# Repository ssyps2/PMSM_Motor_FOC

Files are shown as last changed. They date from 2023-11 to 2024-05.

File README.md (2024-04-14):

## Diode Clamped Converter for Vehicle AC machine Drive

### Aim
The aim of this project is to simulate a 3-Phase Diode Clamped Inverter as a battery connected Permanent Magnet Synchronous Machine (PMSM) drive, and design a PCB to implement a low power version of this type of converter. The control algorithm will be tested in PLECS and eventually implemented in the F28379D micro-controller. Torque, speed, and mechanical position closed loop control of the PMSM motor will be included.

### Simulation
The main topology of the circuit for simulation in the PLECS is shown in Figure below.


### PCB Design
The circuit designed in the simulation will be implemented in a 4-layer Printed Circuit Board (PCB). Surface Mount Technology (SMT) will be applied for more compact layout, higher design flexibility, and reducing the noise interference. The microcontroller is selected to be TI’s LAUNCHXL-F28379D, which is a 32-bit MCU with frequency up to 200MHz and sufficient communication interface (like UART, CAN, I2C) and high-speed PWM channels. Also, current sensor will be used to detect the 3-phase current and sampled by ADC to complete the torque control loop.

The schematic of PCB is shown in Figure below.


The PCB layout is shown in Figrue below.
Diode_Clamped_Inverter_PCB

3D Model:
3D Model_1
3D Model_2

Diode Clamped Inverter:
Diode Clamped Inverter

### TimeTable


### Proposal
[Final Year Project Proposal - Pengyuan SHU.pdf](https://github.com/ssyps2/PMSM_Motor_FOC/files/14595623/Final.Year.Project.Proposal.-.Pengyuan.SHU.pdf)

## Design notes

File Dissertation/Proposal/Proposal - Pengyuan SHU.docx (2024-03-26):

# EEEE3001 / EEEE4008

# Final Year Individual Project Proposal

# Diode Clamped Converter for Vehicle AC machine Drive

AUTHOR: Mr. Pengyuan Shu

ID NUMBER: 20321149

SUPERVISOR: Dr. Alan Watson

MODERATOR: Dr. Gaurang Vakil

DATE: 25 October 2023

Project files and overall progress are available at:

https://github.com/ssyps2/PMSM_Motor_FOC

1. Overview
  1.1 Introduction

In the contemporary landscape characterized by a growing emphasis on clean and sustainable energy sources, the integration of battery-connected Permanent Magnet Synchronous Machine (PMSM) drives assumes a pivotal role across diverse applications, most notably in the domain of electric vehicles. These systems leverage the distinctive architecture of multilevel converters, enabling the generation of multi-level AC voltage waveforms sans the requirement of transformers. Diode Clamped Converter (DCC) is one of the types of multilevel topologies, which is commonly used as drives for high frequency motors as a result of their superior waveform quality [1]. This intrinsic characteristic empowers it to produce high-frequency AC voltages for the PMSM, characterized by notably diminished harmonic distortion. Consequently, the need for extensive filtering and the associated pulsations stemming from these harmonics is substantially reduced.

A fundamental aspect of the PMSM motor is its rotor, which comprises permanent magnets, thus obviating the need for magnetizing current. In this configuration, the motor's torque is solely generated by the stator current. Owing to this inherent efficiency, PMSM motors find widespread application in fields such as robotics and aerospace, where minimizing losses in the rotor is of paramount importance. The control of PMSM motors typically hinges on the Field Oriented Control (FOC) methodology, which can be used to control the AC quantities (voltage, current) [2, 3]. Against this backdrop, the primary focus of this project is to explore the integration of the Diode Clamped Converter into the PMSM drive [4]. For safety reasons, only low-power scenarios (2kW) will be considered. The potential ramifications of this endeavour extend to a wide array of domains, including electric vehicles, renewable energy systems, robotics, and beyond. The successful execution of this project bears the promise of delivering more efficient energy solutions, and in so doing, opens the door to fresh commercial opportunities and contributes to broader economic growth.

  1.2 Aim

The aim of this project is to simulate a 3-Phase Diode Clamped Inverter as a battery connected Permanent Magnet Synchronous Machine (PMSM) drive, and design a PCB to implement a low power version of this type of converter. The control algorithm will be tested in PLECS and eventually implemented in the F28379D micro-controller. Torque and speed closed loop control of the PMSM motor will be included.

  1.3 Objectives
A. Simulation

The main topology of the circuit for simulation in the PLECS is shown in Figure 1.

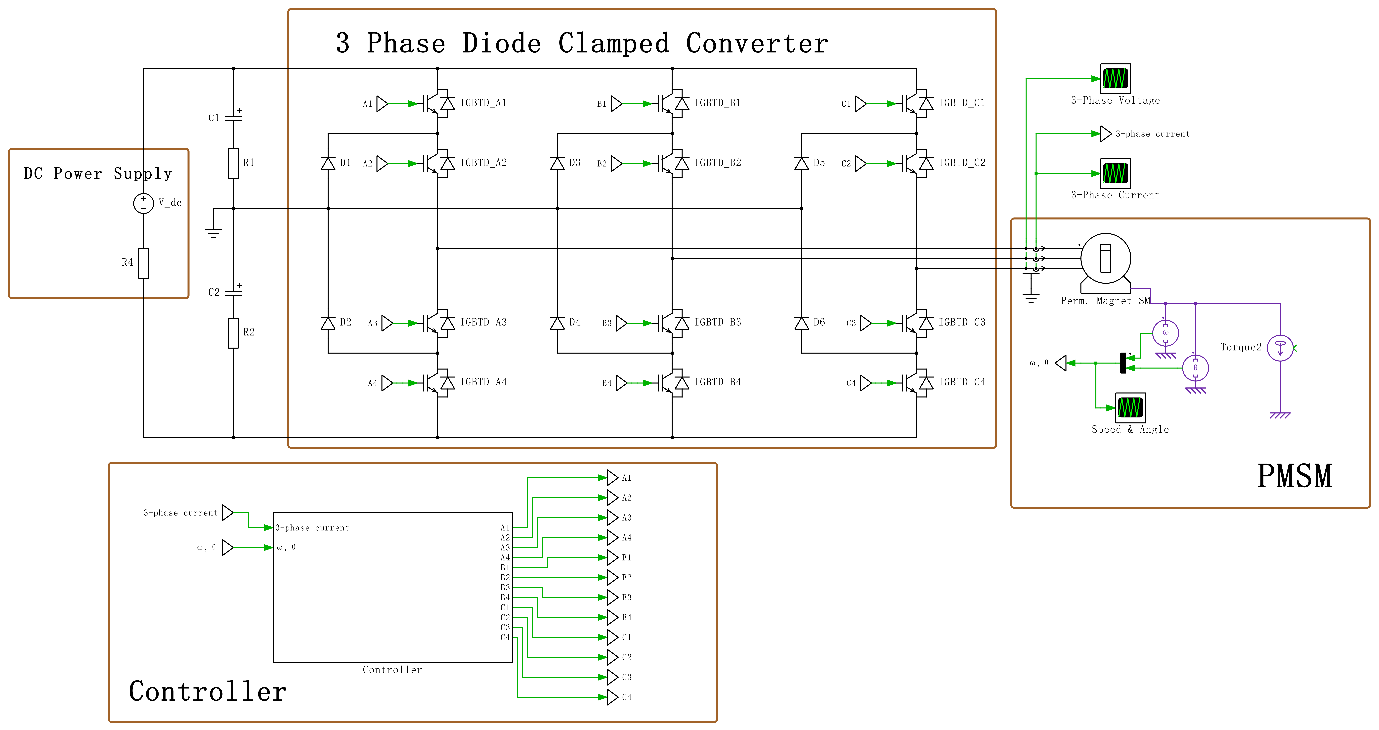
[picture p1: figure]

Figure 1. Main Topology for Simulation

B. PCB Design

The circuit designed in the simulation will be implemented in a 4-layer Printed Circuit Board (PCB), which is a medium used to integrate all the electrical components. Surface Mount Technology (SMT) will be applied for more compact layout, higher design flexibility, and reducing the noise interference. The microcontroller is selected to be TI’s LAUNCHXL-F28379D, which is a 32-bit MCU with frequency up to 200MHz and sufficient communication interface (like UART, CAN, I2C) and high-speed PWM channels. Also, current sensor will be used to detect the 3-phase current and sampled by ADC to complete the torque control loop.

2. Specification
  2.1 Software

The controller takes the 3-phase current and PMSM motor’s angle and speed as input, and output the PWM for each IGBT in the diode clamped converter. The controller contains two closed loops in series: torque loop and speed loop. The most fundamental loop is torque loop, which also can be referred to as current loop, as the torque of the PMSM motor is proportional to its stator current. This is where the FOC algorithm can be applied, combined with the PI controller to control the three-phase current in a closed loop to generate target torque based on the mechanical position of the rotor. Building upon the foundation of torque closed loop, the speed loop can be implemented by using the serial PI controller.

  2.2 Hardware

The specification for 3 phase PMSM motor would be like:

Power Rating | 2kW
Frequency Rating | 50Hz/60Hz
Supply Voltage | 300-320V

  2.3 Criteria for Success
a. PCB has no significant heating and vibration noise during operation.
b. Clear and correct 3 phase waveforms of both simulation and practical testing results.
c. Torque and speed of PMSM motor can be fully controlled by Qt-based HMI.
3. Methodology

No. | Goals and Processes | Challenges
1 | Read related resources to get familiar with the diode clamped converters and PMSM drives. | NA
2 | [Hardware] Select components according to the requirements (manufacturers can be Mouser, RS, Farnell…). The process is basically applying filter to exclude most irrelevant options, and compare those roughly fitted, then choose and order the best fit one (cheap / low loss / high tolerant…). | Some components might be unavailable / too expensive / take too long to ship
3 | [Hardware] Draw schematics based on selected components in KiCad, assign footprints to each component, and draw footprints that cannot found in the library. | Techniques for voltage balance between capacitors should be considered to prevent distortion.
4 | [Hardware] Plan PCB layout in KiCad, draw traces (ensure they are wide enough to handle large current) to connect components. Send project files to PCB factory for manufacturing. | Applying the design principles to reduce noise (should or should not use vias; thermal management on board; how to avoid ground bounce…)
5 | [Software] Whilst PCB is being manufactured, construct the diode clamped converter and the PMSM model in PLECS (fill up the parameters of PMSM simulation model according to the real machine model). | Mathematic modelling might be hard to implement; PMSM simulation model may not fit the real machine model well.
6 | [Software] Simulate the FOC algorithm and close the torque control loop in PLECS. Adjust the parameters to get expected output. | Implementation of FOC; Parameters of discrete PI controller might be difficult to tune.
7 | [Software] Further accomplish the speed closed loop control in PLECS. Adjust the parameters to get expected output. | Parameters tuning of discrete serial PI controller.
8 | [Hardware] Solder all the components to complete the converter construction, and test it with DC power source. | Small surface mount package components might be hard to solder on pads.
9 | [Software] Use Code Composer Studio (CCS) and Digital Power SDK to construct the embedded C code to implement the control algorithm on MCU, and validate simulation work with PCB connected to an RL load. | Task frequency will affect the parameters of PI controllers.
10 | Stretch target 1: Use the PCB to drive a low power PMSM motor with full FOC. | Realistic constrains of PMSM motor; Motor’s feedback data need to be logged and plotted.
11 | Stretch target 2: Design a Qt based human-machine interface (HMI) with a joystick for sending control commands to achieve torque and speed control of PMSM motor on a PC. | Delay might be occurred in data transmission, which will have negative impact on control.

4. Time Plan

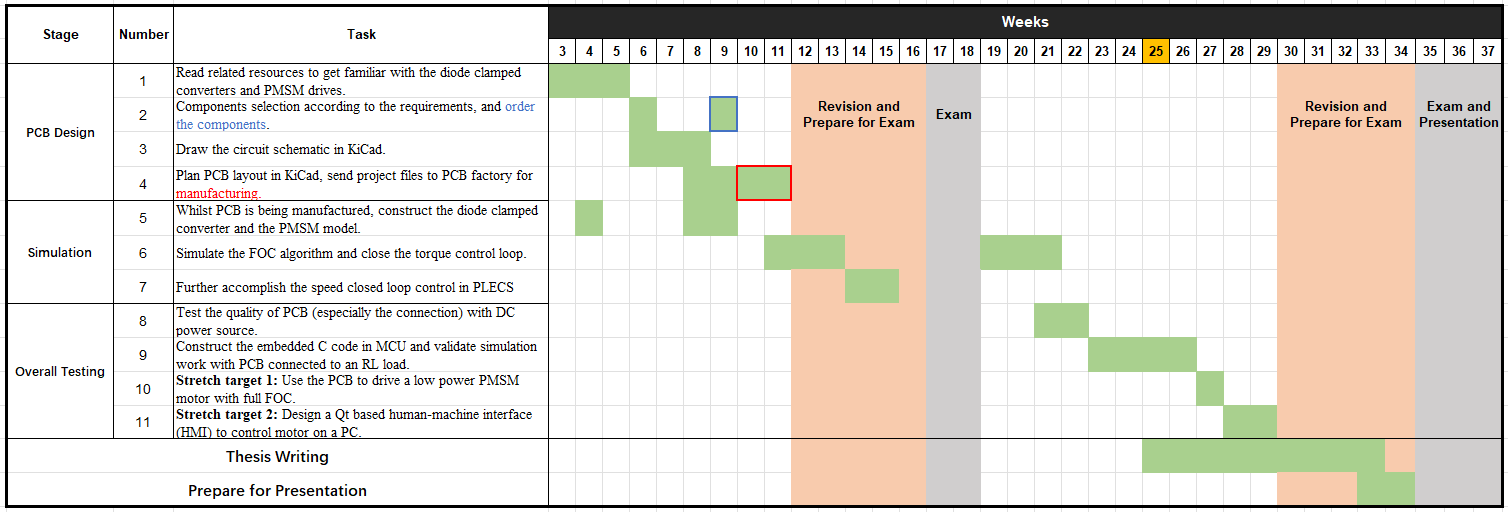
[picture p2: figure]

5. Reference

[1] B. Wu, “High Power Converters and AC Drives”, Wiley IEEE, 2nd Edition, 2016

[2] G. Abad, “Power Electronics and Electric Drives for Traction Applications”, Wiley, 2016

[3] A. Hughes “Electric Motors and Drives: Fundamentals, types, and applications”, 5th Edition, Elsevier, 2019

[4] S. N. Vukosavic, “Electrical Machines”, Springer, 2012

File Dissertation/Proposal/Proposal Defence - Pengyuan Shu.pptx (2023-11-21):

## Diode Clamped Converter for Vehicle AC Machine Drive

Pengyuan Shu (20321149)

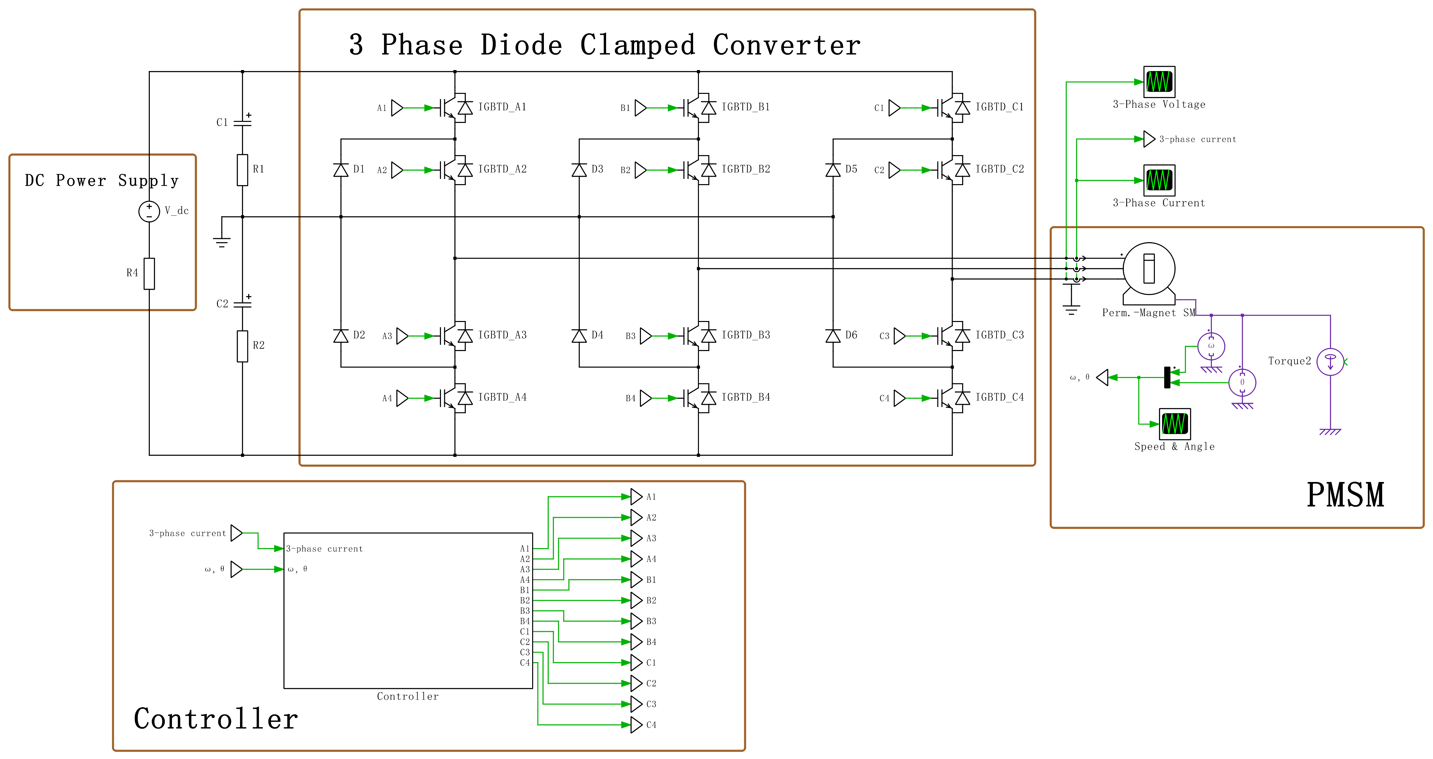
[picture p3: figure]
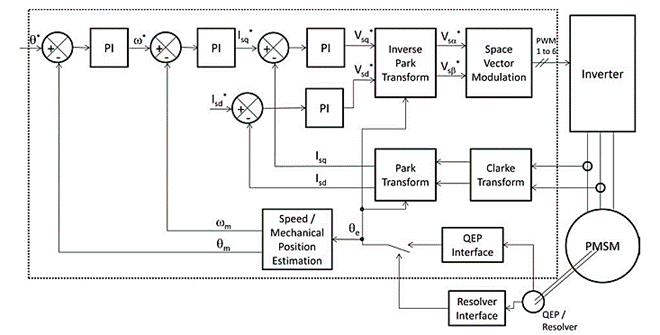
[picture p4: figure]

Circuit Topology

Control Diagram

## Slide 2

Methods and Approach

No. | Goals and Processes | Challenges
1 | Read related resources to get familiar with the diode clamped converters and PMSM drives. | NA
2 | Select components according to the requirements (manufacturers can be Mouser, RS, Farnell…). The process is basically applying filter to exclude most irrelevant options, and compare those roughly fitted, then choose and order the best fit one (cheap / low loss / high tolerant…). | Some components might be unavailable / too expensive / take too long to ship
3 | Draw schematics based on selected components in KiCad, assign footprints to each component, and draw footprints that cannot found in the library. | Techniques for voltage balance between capacitors should be considered to prevent distortion.
4 | Plan PCB layout in KiCad, draw traces (ensure they are wide enough to handle large current) to connect components. Send project files to PCB factory for manufacturing. | Applying the design principles to reduce noise (should or should not use vias; thermal management on board; how to avoid ground bounce…)
5 | Whilst PCB is being manufactured, construct the diode clamped converter and the PMSM model in PLECS (fill up the parameters of PMSM simulation model according to the real machine model). | Mathematic modelling might be hard to implement; PMSM simulation model may not fit the real machine model well.
6 | Simulate the FOC algorithm and close the torque control loop in PLECS. Adjust the parameters to get expected output. | Implementation of FOC; Parameters of discrete PI controller might be difficult to tune.
7 | Further accomplish the speed and mechanical position closed loop control in PLECS. Adjust the parameters to get expected output. | Parameters tuning of discrete serial PI controller.
8 | Solder all the components to complete the converter construction and test it with DC power source. | Small surface mount package components might be hard to solder on pads.
9 | Use Code Composer Studio (CCS) and Digital Power SDK to construct the embedded C code to implement the control algorithm on MCU and validate simulation work with PCB connected to an RL load. | Task frequency will affect the parameters of PI controllers.
10 | Stretch target 1: Use the PCB to drive a low power PMSM motor with full FOC. | Realistic constrains of PMSM motor; Motor’s feedback data need to be logged and plotted.
11 | Stretch target 2: Design a Qt based human-machine interface (HMI) with a joystick for sending control commands to achieve torque / speed / mechanical position control of PMSM motor on a PC. | Delay might be occurred in data transmission, which will have negative impact on control.

## Risk Table

Potential Risks | Mitigation Actions | Likelihood | Severity
PCB may not be manufactured as scheduled due to chip shortage or other unknown accidents. | Complete the schematic and PCB layout, then send them to factory for manufacturing early in the project. | Medium | High
Some key components are unavailable / shipping takes too long / too expensive. | Find alternatives, and identify those “long lead time” components | High | Low
The PCB may be damaged (e.g., burned), or contain a lot of noise interference due to design flaws. | Check the PCB layout with care (or ask supervisor for advice) before sending it to manufacture to prevent significant flaws. Adopt redundant design. Ensure the traces that can pass large current are wide enough. | Medium | High
Component size does not fit the package in the PCB. | Check the package size of each component before sending the PCB to manufacture. | Low | High
The performance of applied algorithm is less satisfactory. | Use MATLAB to evaluate the stability of the controller, modify it or adopt other controllers. | Medium | Medium

## Time Plan

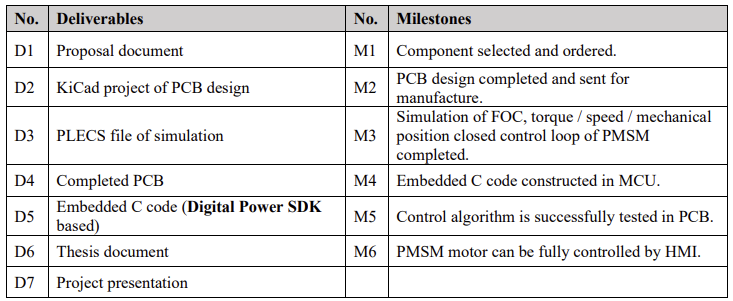
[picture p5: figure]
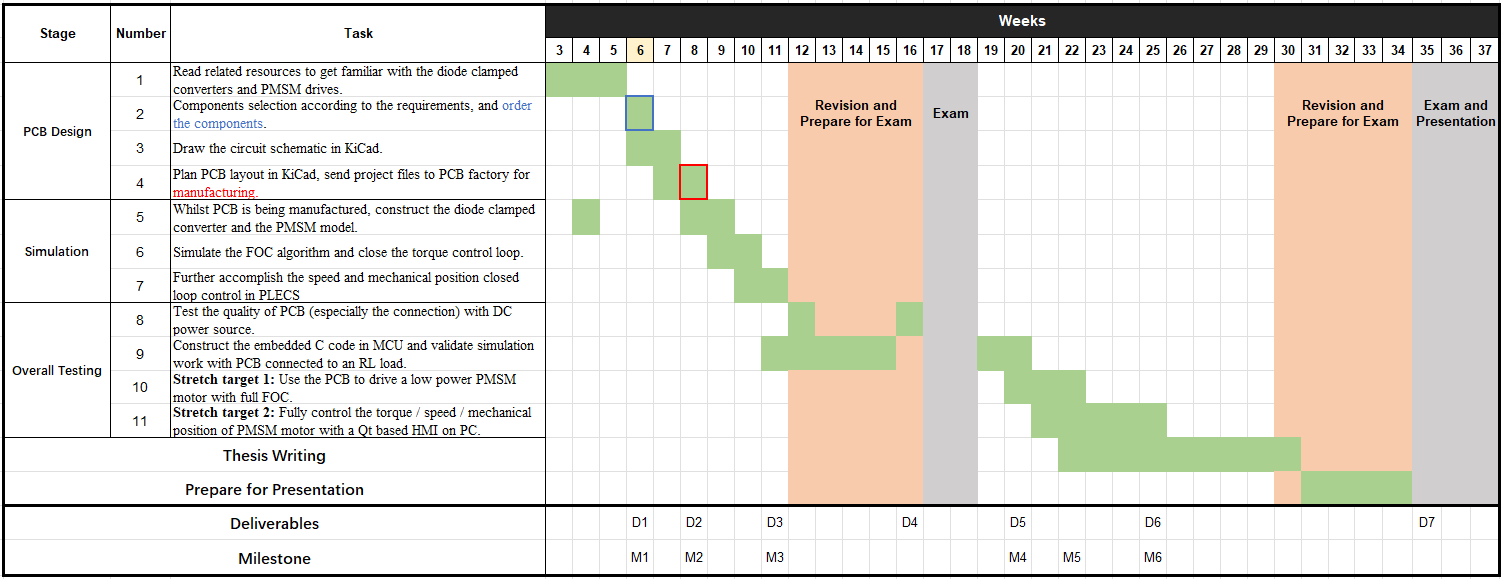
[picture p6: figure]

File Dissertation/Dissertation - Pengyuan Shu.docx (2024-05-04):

# EEEE3001

# Final Year Individual Project Dissertation

# Diode Clamped Inverter for Vehicle AC Machine Drive

AUTHOR: Mr. Pengyuan Shu

ID NUMBER: 20321149

SUPERVISOR: Dr. Alan Watson

MODERATOR: Dr. Gaurang Vakil

DATE: 9 May 2024

This third year project Dissertation is submitted in part fulfilment of the requirements of the degree of Bachelor of Engineering.

Table of Contents

Abstract (1 pages)

Chapter 1: Introduction (3 pages)

  1.1 Background and Summary of Literature Review

1.2 Aims and Objectives

Chapter 2: Simulation and Controller Design (15 pages)

2.1 Specifications of Tool Choice

2.2 PMSM Motor Modelling

2.3 Field-Oriented Control (FOC)

2.4 Topology Overview and Control Diagram

2.5 SPWM and SVPWM

2.6 Design of Controllers

Chapter 3: Hardware Design: Diode Clamped Inverter (6 pages)

3.1 Schematic

3.2 DC-Link Capacitance Calculations

3.3 Loss Calculations

3.4 PCB Layout

3.5 Physical Product

Chapter 4: Hardware Design: Control Board and its Peripherals (2 pages)

4.1 Schematic and PCB Layout

4.2 ADC Sampling

4.3 Physical Product

Chapter 5: Software Design: Implementation on MCU (6 pages)

5.1 Files Structure and IDE Configurations

5.2 Algorithm Implementation

Chapter 6: System Testing, Validation, and Analysis (8 pages)

6.1 Testing and Validation

6.2 Results Analysis

Chapter 7: Conclusion and Reflection (4 pages)

7.1 Consideration of System within Wider Context

7.2 Reflection on Management

References

Appendix

Abstract

Chapter 1: Introduction

  1.1 Background and Summary of Literature Review
    1.1.1 Introduction to PMSM

Permanent Magnet Synchronous Machines (PMSMs) are a class of electric motors that utilize permanent magnets embedded in the surface of the motor's rotor. This design is fundamental in creating a magnetic field that synchronizes with the rotating magnetic field of the stator. Efficiency is one of the distinguishing characteristics of PMSMs; the permanent magnets provide a steady magnetic field without the stator current, which is normally needed in other kinds of motors to maintain the field via the rotor windings.

The PMSM stands out for its high-power density, which is the amount of power generated per unit volume of the motor. This feature is particularly beneficial in the applications where space and weight are constrained, such as in automotive or aerospace industries. Another advantage of PMSMs is their high operational efficiency throughout a wide range of speeds and loads. This adaptability is complemented by their remarkable torque-to-weight ratio, which allows them to produce more torque per unit of motor weight than many other motor types. Moreover, PMSMs are also noted for their quiet operation and low maintenance requirements due to the lack of brushes and slide rings, which are prone to wear and strain.

The PMSM's torque generation capability is a direct consequence of the electromagnetic interaction between the stator's rotating magnetic field and the rotor's permanent magnets. This interaction produces torque that is precisely controllable, which is why PMSMs are ideal candidates for variable speed and position control applications.

    1.1.2 Introduction to Diode Clamped Inverter

The diode clamped inverters, also known as Neutral Point Clamped (NPC) inverters, can convert direct current (DC) to alternating current (AC) in a variety of applications. They are characterized by their multilevel output, which can generate voltage waveforms with steps at several voltage levels, not just the two levels produced by traditional two-level inverters. This ability to approximate sinusoidal waveforms more closely results in lower total harmonic distortion (THD). Due to their superior waveform quality, these types of inverters are commonly used as the drives for high frequency motors [1]. This intrinsic feature enables it to generate high-frequency AC voltages for the PMSM with significantly less harmonic distortion, and thus, the pulsations caused by these harmonics is significantly reduced.

In the three-phase diode clamped inverter topology, each phase leg includes several power semiconductor switches (could be MOSFET or IGBT) and clamping diodes. The clamping diodes are critical components that allow the inverter to maintain the voltage balance of the DC-link capacitors during operation, thereby ensuring the generation of the desired multi-level AC waveform. In this project, a three-phase three-level diode clamped inverter is used as the drive of PMSM motor, the topology is shown in the Figure 1.1 below. Three-level means each phase of the inverter can generate three different levels of voltage, which are +V_(dc) /2 , 0V, and -V_(dc) /2 .

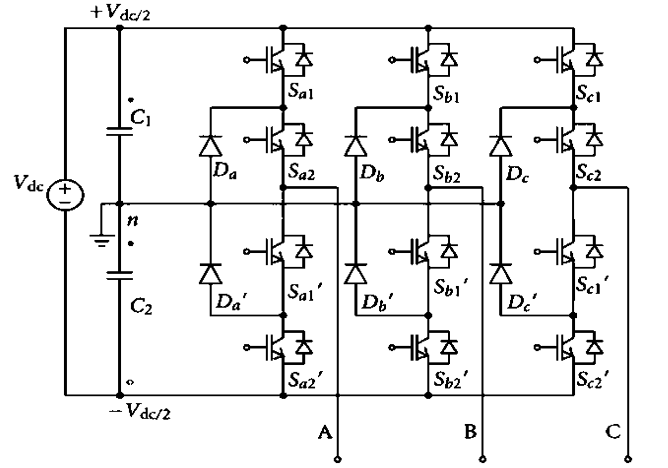
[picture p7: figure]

Figure 1.1 Topology of Three-Phase Three-Level Diode Clamped Inverter

    1.1.3 Field-Oriented Control (FOC)

Field-Oriented Control (FOC), also known as vector control, is an advanced method of motor control that treats the electric motor as a controllable entity in two orthogonal components [2, 3]. This control technique allows for separate control of the magnetic flux and torque in AC machines (such as PMSM), by aligning the reference frame of the control system with the vector space of the motor’s magnetic field. Essentially, FOC decouples the PMSM's torque and magnetic flux into two independent variables that can be controlled as if the motor were a direct current (DC) motor.

    1.1.4 Review of Existing Technologies and Developments

Inverter technology has advanced significantly, especially in the area of electric vehicle (EV) propulsion. Innovations in semiconductor materials, such as Silicon Carbide (SiC) and Gallium Nitride (GaN), have been critical in spawning a new generation of inverters. These new inverters offer increased power densities and efficiency, as well as the extraordinary ability to perform optimally at high frequencies and temperatures. The consequence is a significant reduction in the physical bulk and weight of inverter systems, as well as an increase in their dependability and operational lifespan.

Meanwhile, for control algorithm, there is also a technique called sensorless control, which eliminate the need for physical sensors in the motor by using estimators and observers to infer the rotor position. However, due to the complexity of algorithm, and issue of robustness, it would not be covered in this report.

  1.2 Aims and Objectives

The aim of this project is to achieve current and speed control of the PMSM motor (300V, BSM90N-175) through a three-phase three-level diode clamped inverter in PLECS and in reality. The inverter is controlled by TI’s F28379D Launchpad. For safety concerns, only low power situation (2kW) would be considered.

The project can be divided into following stages:

Stage 1: Initial Simulation of FOC in PLECS

Aim:

Create a mathematical model of PMSM motor in PLECS, and implement FOC in PLECS to verify the minimum acceptable capacitance of the DC-link capacitors.

Objectives:

- Work out the mathematical model of BSM90N-175 motor.
- Learn the working principles of Field-Oriented Control, build the continuous control model in PLECS.
- Change the target torque current to verify the performance of the two DC-link capacitors with calculated capacitance value, then work out the minimum acceptable value of capacitance and find the most suitable capacitor on the market.

Stage 2: Hardware Design in KiCad and Manufacturing

Aim:

Design a four-layer printed circuit board (PCB) for the three-phase three-level diode clamped inverter, as well as design a two-layer PCB for the control board (F28379D Launchpad) and its peripherals.

Objectives:

- Selection of components, build bill-of-materials (BOM) lists for purchasing.
- Schematic of the control board and the board of diode clamped inverter in KiCad, which includes gate drive circuit, ADC sampling circuit, connectors, etc.
- PCB layout in KiCad.

Stage 3: Controller Design in PLECS and MATLAB

Aim:

Design the continuous PI controller of speed, DC voltage balancing, and d-axis and q-axis current in MATLAB, convert them to discrete controllers and test in PLECS.

Objectives:

- Transfer functions of these continuous PI controllers from the “sisotool” in MATLAB.
- Convert the continuous PI controllers to discrete PI controllers.
- Test the discrete PI controller in PLECS.
- Convert the function blocks to “c-script” blocks in PLECS.

Stage 4: Software Design in Code Composer Studio (CCS)

Aim:

Convert the control algorithm and overall logic in PLECS file to C code that can be built and loaded on TMS320F28379D micro-controller, then test the program in real PMSM motor to verify the current and speed control.

Objectives:

- Configurate the environment of CCS, including file search path, library search path, predefined symbols, optimization configurations, etc.
- Construction of CCS program, which includes ADC sampling, motor encoder decoding, PI controller implementation, timer interruption, SPWM generation, etc.
- Test the program in real BSM90N-175 motor with the two PCBs to verify the speed and current control.

Chapter 2: Simulation and Controller Design

2.1 Specifications of Tool Choice

PLECS (Piecewise Linear Electrical Circuit Simulation) is chosen to be the tool of circuit simulation. It is a better choice than MATLAB in simulating electrical circuits for following reasons:

- PLECS can offer faster simulation times due to its optimized solvers.
- PLECS can offer real-time simulation capabilities for hardware-in-the-loop (HIL) testing. This feature is useful for testing the control logic on actual hardware before deployment.
- PLECS provides integrated thermal modelling, which enables the simulation of temperature-dependent behaviours of components and systems.

However, PLECS is not a suitable tool for controller design. For PI controller design, a tool named “sisotool” in MATLAB is used, which is an interactive graphical user interface (GUI) tool for designing and analysing single-input, single-output (SISO) control systems. It offers a variety of plotting functions, including bode plots, root locus, and step response plots, which are essential for understanding the frequency and time domain characteristics of the system.

2.2 PMSM Motor Modelling

The model is chosen to be ABB’s BSM90N-175. The electrical and mechanical parameters of this motor are shown in Table 2.1 below.

Table 2.1 Parameters of BSM90N-175 Model

Rated Speed (at 300 V) | 4000 rpm
Torque Constant K_t | 0.853 Nm/amp
Stator Resistance R_s | 1.24 ohms
Stator Inductance L_s | 4.15 mH
Pole Pairs p | 4
Inertia J | 3.389 Kg- cm^2

The electrical model of PMSM in PLECS is modelled by:

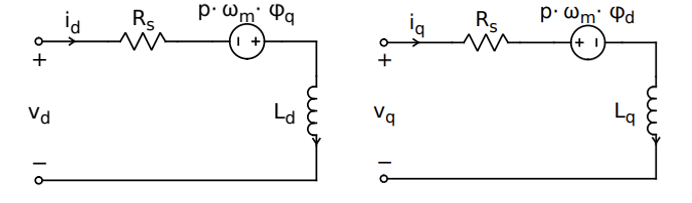
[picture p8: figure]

Figure 2.1 Electrical Model of PMSM in PLECS (left: d-axis; right: q-axis)

The stator flux linkages are given by:

φ_q =L_q i_q Eqn.2.1

φ_d =L_d i_d +φ_m^(') Eqn.2.2

where the symbol φ_m^(') represents the constant flux linkage, the symbol L_d and L_q represent stator inductance in d-axis and q-axis.

The three-phase stator currents are transformed to the two-dimensional rotating reference dq-frame, which converts an AC system into an equivalent DC system. This enables the use of traditional PI controllers with zero steady-state error. According to Figure 2.1, the stator voltage in d-axis and q-axis are given by:

V_d =R_s i_d -pω_m φ_q +L_d (di_d)/(dt) Eqn.2.3

V_q =R_s i_q +pω_m φ_d +L_q (di_q)/(dt) Eqn.2.4

Due to the AC motor is a synchronous machine with surface-mounted magnets and no saliency, flux lines are distributed evenly around the stator, which means that the motor's inductance measured in the direction of the d-axis and the q-axis will be the same. Thus:

L_q =L_d Eqn.2.5

This equality leads to a simplified Field-Oriented Control algorithm, because the current-regulating controller does not have to compensate for differences in inductance in different orientations of the rotor. As they are equal, L_q and L_d can be represented by L_s . Thus, Eqn.2.3 and Eqn.2.4 can be rearranged as:

V_d =R_s i_d -ω_e L_s i_q +L_s (di_d)/(dt) Eqn.2.6

V_q =R_s i_q +ω_e (L_s i_d +φ_m^(') )+L_s (di_q)/(dt) Eqn.2.7

where the electrical rotor speed ω_e =pω_m .

Moreover, according to the manual of PLECS, electromagnetic torque T_e and mechanical rotor speed ω_m of PMSM model in PLECS are given by:

T_e =3/2p(φ_d i_q -φ_q i_d ) Eqn.2.8

ω_m =1/J(T_e -Bω_m -T_m ) Eqn.2.9

ω_m =θ_m Eqn.2.10

where the symbol B represents the friction coefficient.

The configurations of initialising PMSM in PLECS are presented in Figure 2.2 and Figure 2.3 below, whose data are referred from the datasheet of BSM90N-175 motor. The model of PMSM is chosen to be “Rotor reference frame”, as it can decouple the motor’s flux and torque. In addition, the friction coefficient is assumed to be zero for simplification.

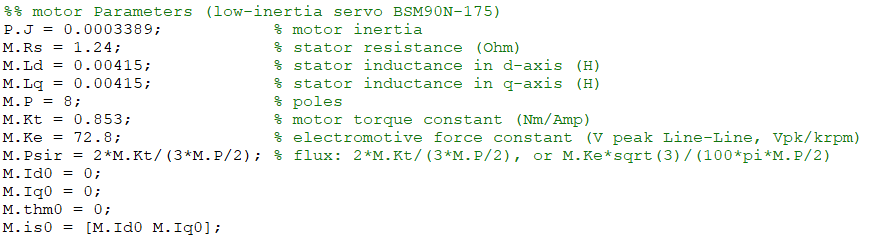
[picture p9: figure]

Figure 2.2 C-Code for Simulation Parameter Initialization in PLECS

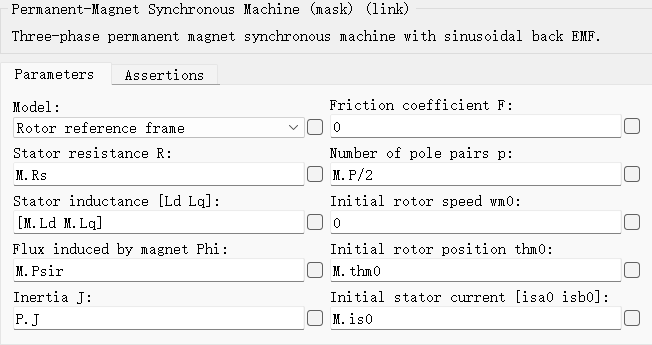
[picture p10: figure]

Figure 2.3 Configurations of PMSM Model in PLECS

2.3 Field-Oriented Control (FOC)

Field-Oriented Control is a control technique used in variable frequency drives to control the torque (and thus speed and position) of three-phase AC electric motors by controlling the current components independently. The essence of this algorithm is to decompose the stator currents into two orthogonal components that can be controlled separately: one aligns with the rotor's magnetic field (direct axis, or d-axis), and the other is perpendicular to it (quadrature axis, or q-axis). This decomposition allows the control system to adjust the torque and magnetic flux of the motor independently, like DC motor, which is easier to control because torque is directly controlled by armature current.

The procedures of FOC are demonstrated as follows:

1. Sample the phase currents of PMSM and get I_a , I_b , and I_c .
2. Convert I_a , I_b , I_c to I_α , I_β via Clarke Transformation.
3. Convert I_α , I_β to I_q , I_d via Park Transformation.
4. Calculate the errors between measured I_q , I_d and target I_q , I_d , enter the errors to two PI controllers and get control voltage V_q , V_d .
5. Convert V_q , V_d to V_α , V_β via Inverse Park Transformation.
6. Convert V_α , V_β to V_a , V_b , V_c via Inverse Clarke Transformation, and enter the three-phase voltage to Sinusoidal Pulse Width Modulation (SPWM) module to output PWM for each gate according to the position of rotor. Another alternative is using V_α , V_β to synthetic voltage space vector and enter the Space Vector PWM (SVPWM) module to obtain PWM for each gate.
7. Repeat above procedure in switching frequency.

The control diagram of FOC is shown in Figure 2.4 below.

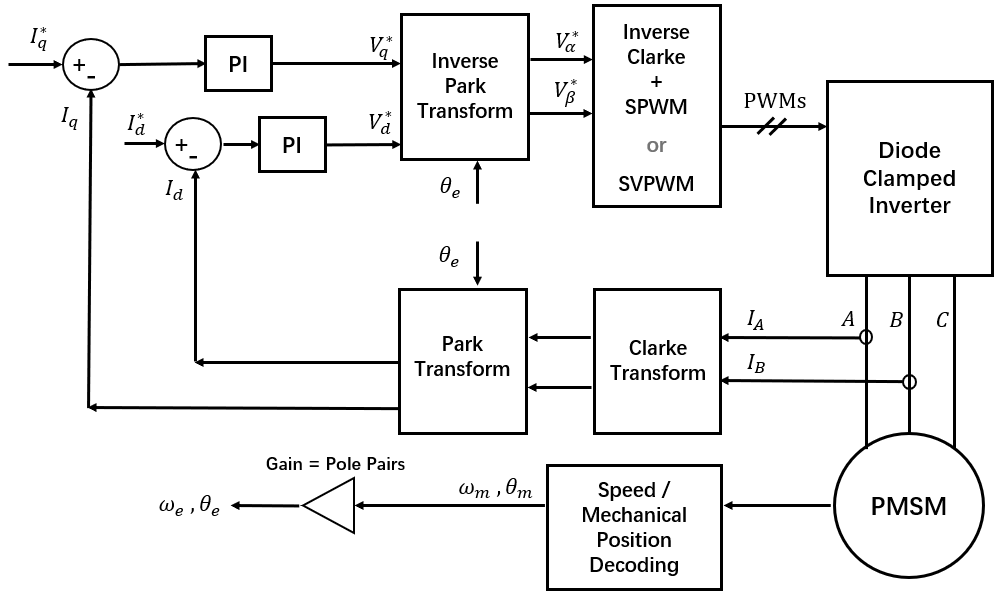
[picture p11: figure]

Figure 2.4 Control Diagram of FOC

Clarke Transformation

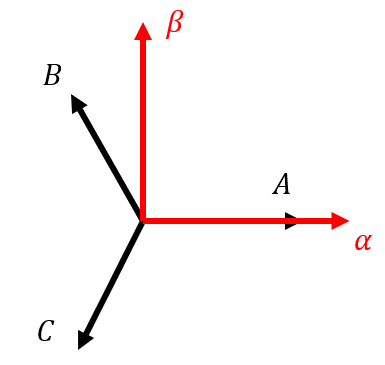
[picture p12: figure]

Figure 2.5 ABC-Frame and α β Frame

The first step of Clarke Transformation is projection:

I_α =I_a -1/2I_b -1/2I_c Eqn.2.11

I_β =(√3)/2I_b -(√3)/2I_c Eqn.2.12

Thus, the relationship of I_a , I_b , I_c and I_α , I_β can be expressed by:

[I_α I_β ]=[1, -1/2, -1/20, (√3)/2, -(√3)/2][I_a I_b I_c ] Eqn.2.13

The second step is to convert Eqn.2.13 to scaled version. According to Kirchhoff's current law, the sum of I_a , I_b , I_c should be zero:

I_a +I_b +I_c =0 Eqn.2.14

Assume I_a =1 A , then I_b =I_c =-0.5 A , the value of I_α and I_β would be:

[I_α I_β ]=[1, -1/2, -1/20, (√3)/2, -(√3)/2][1-1/2-1/2 ]=[3/20] Eqn.2.15

Although the vector I_a and I_α are overlapped, the projection of I_b and I_c make them not equal. Therefore, to make them equal, the Eqn.2.13 should be scaled by 2/3.

[I_α I_β ]=2/3[1, -1/2, -1/20, (√3)/2, -(√3)/2][I_a I_b I_c ] Eqn.2.16

According to Eqn.2.14, I_c =-I_a -I_b , which means I_c does not need to be sampled. I_α and I_β could be expressed by:

I_α =I_a Eqn.2.17

I_β =1/(√3)(I_a +2I_b ) Eqn.2.18

Inverse Park Transformation

Rearrange the Eqn.2.14, Eqn.2.17 and Eqn.2.18, phase current I_a , I_b , I_c could be given by:

I_a =I_α Eqn.2.19

I_b =(√3I_β -I_α)/2 Eqn.2.20

I_c =(-√3I_β -I_α)/2 Eqn.2.21

Park Transformation

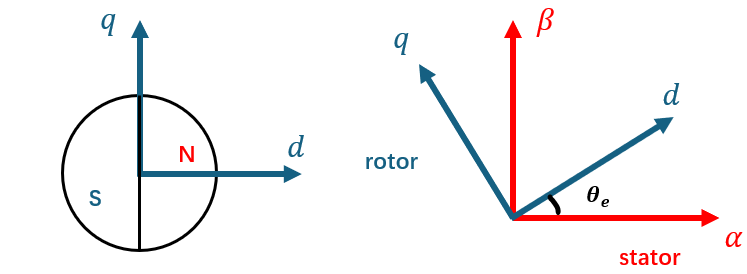
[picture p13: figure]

Figure 2.6 α β Frame and dq-Frame

The symbol θ_e represents the electrical angle of rotor, which equals the result of number of pole pairs multiplied by mechanical rotor angle. The relationship of I_d , I_q and I_α , I_β can be given by:

[I_d I_q ]=[cosθ_e , sinθ_e -sinθ_e , cosθ_e ][I_α I_β ] Eqn.2.22

I_d =I_α ∙cosθ_e +I_β ∙sinθ_e Eqn.2.23

I_q =I_α ∙(-sinθ_e )+I_β ∙cosθ_e Eqn.2.24

Inverse Clarke Transformation

Rearrange Eqn.2.22:

[I_α I_β ] =[cosθ_e , sinθ_e -sinθ_e , cosθ_e ]^(-1) [I_d I_q ] Eqn.2.25

Then I_α and I_β can be given by:

I_α =I_d ∙cosθ_e -I_q ∙sinθ_e Eqn.2.26

I_β =I_d ∙sinθ_e +I_q ∙cosθ_e Eqn.2.27

2.4 Topology Overview and Control Diagram

Each phase of the inverter contains four IGBTs (with diode) to control the voltage level between S2 and S3 by switching. The other two diodes in each phase help in maintaining the voltage balance across the two DC-link capacitors.

The truth table of switching is presented in Table 2.2 below.

Table 2.2 Truth Table of Phase Voltage

Phase Voltage | S1 | S2 | S3 | S4
+U_(dc) /2 | 1 | 1 | 0 | 0
0 | 0 | 1 | 1 | 0
-U_(dc) /2 | 0 | 0 | 1 | 1

It can be observed from the Figure 1.1 that there are two DC-link capacitors between DC voltage source and IGBT bridges. The two capacitors are not only used for dividing the DC voltage, but also act as a decoupling element between the power supply (which may include batteries, photovoltaic arrays, or rectifiers) and the inverter. It helps to minimize the injection of harmonics back into the power source and also reduces the harmonic content in the output AC waveform.

The controller takes the 2-phase current and PMSM motor’s angle and speed as input, and output the PWMs for each IGBT in the inverter. The controller contains three closed control loops: the current control loop contains two parallel loops (d-axis and q-axis), and speed control loop is in series with the q-axis current control loop. The current loop can also be referred as the torque loop because the torque of PMSM motor is proportional to its stator current. This is where the FOC algorithm can be applied, combined with the PI controllers to control the three-phase current and voltage to generate target torque according to the position of the rotor.

The main topology of the circuit for simulation in the PLECS is shown in Figure 2.7 below.

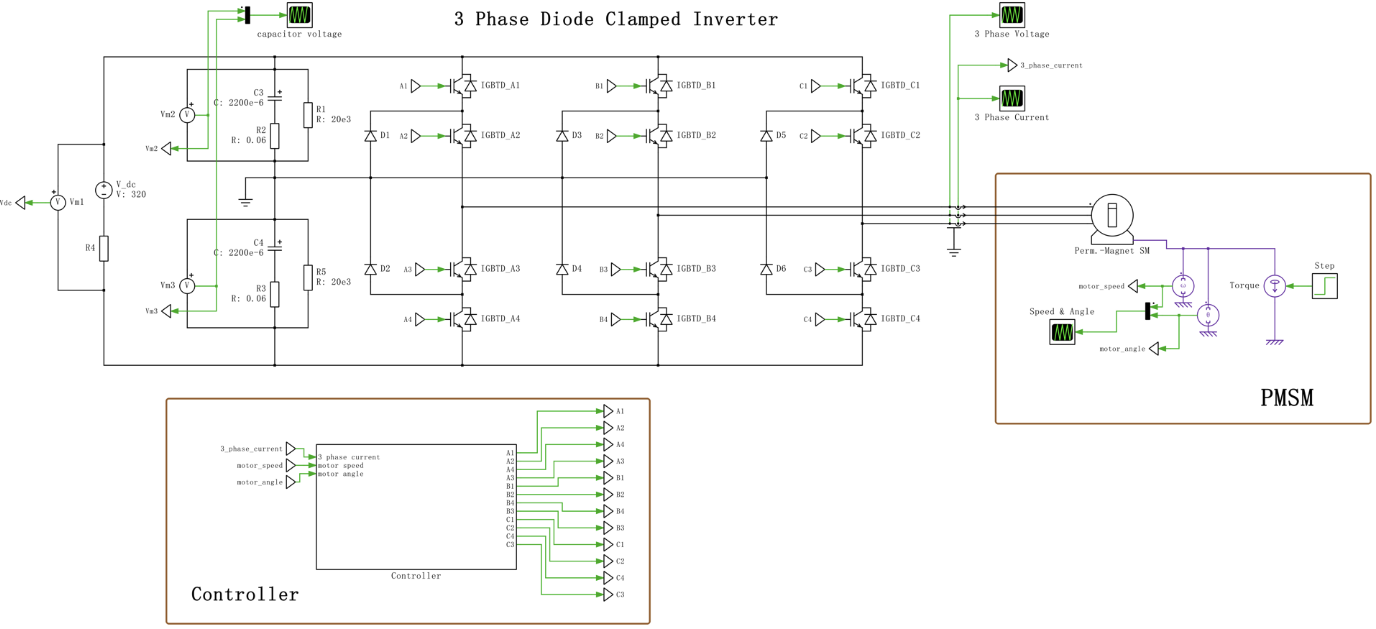
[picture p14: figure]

Figure 2.7 Main Topology of Simulation

The 20k ohms resistors that connected in parallel with the DC-link capacitors can help balance the voltage across each capacitor. Moreover, when the system is turned off, the capacitors can hold a charge for a significant amount of time. The resistors provide a discharge path for the stored energy, ensuring that the capacitors discharge safely and relatively quickly, which is important for maintenance and safety reasons.

According to Eqn.2.6 and Eqn.2.7, the transformation from the three-phase to the dq-frame brings cross-coupling between the d-axis and the q-axis, which have to be considered in the controller structure. Therefore, the overall control diagram is shown in the Figure 2.8 below.

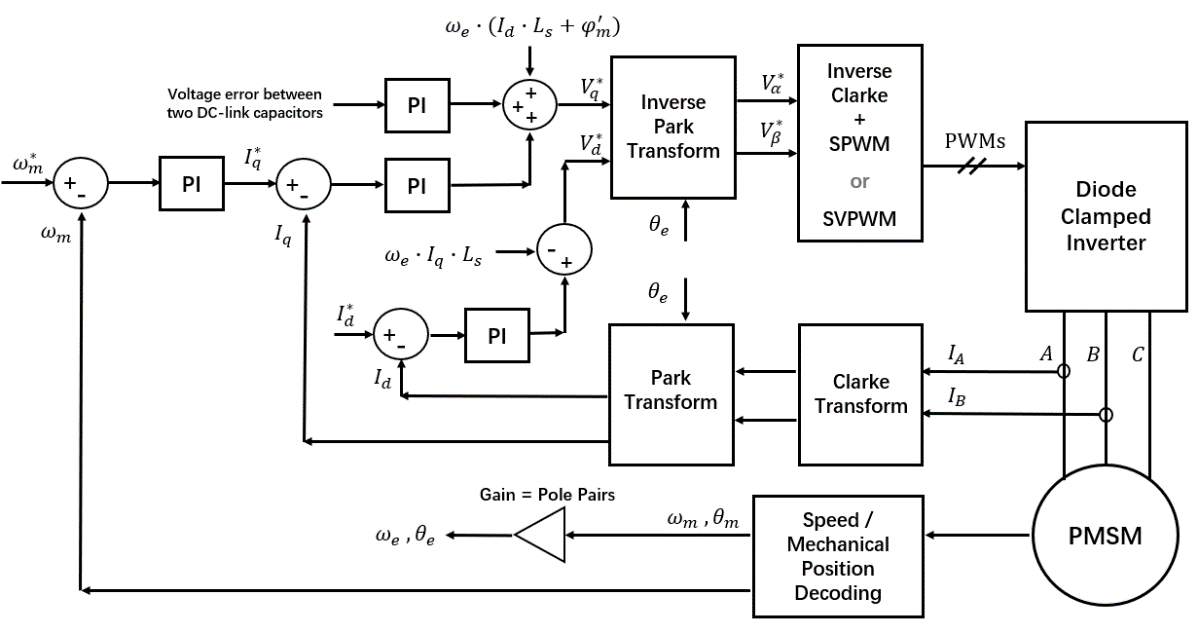
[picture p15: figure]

Figure 2.8 Overall Control Diagram

2.5 SPWM and SVPWM

2.5.1 Sinusoidal PWM (SPWM)

The basic idea behind SPWM is to control the output voltage by modulating the width of the pulses based on a sinusoidal reference signal. The resulting PWM waveform effectively modulates the average voltage over time to approximate a sinusoidal AC output from a DC input. The three-phase SPWM is constructed as Figure 2.9 in the simulation.

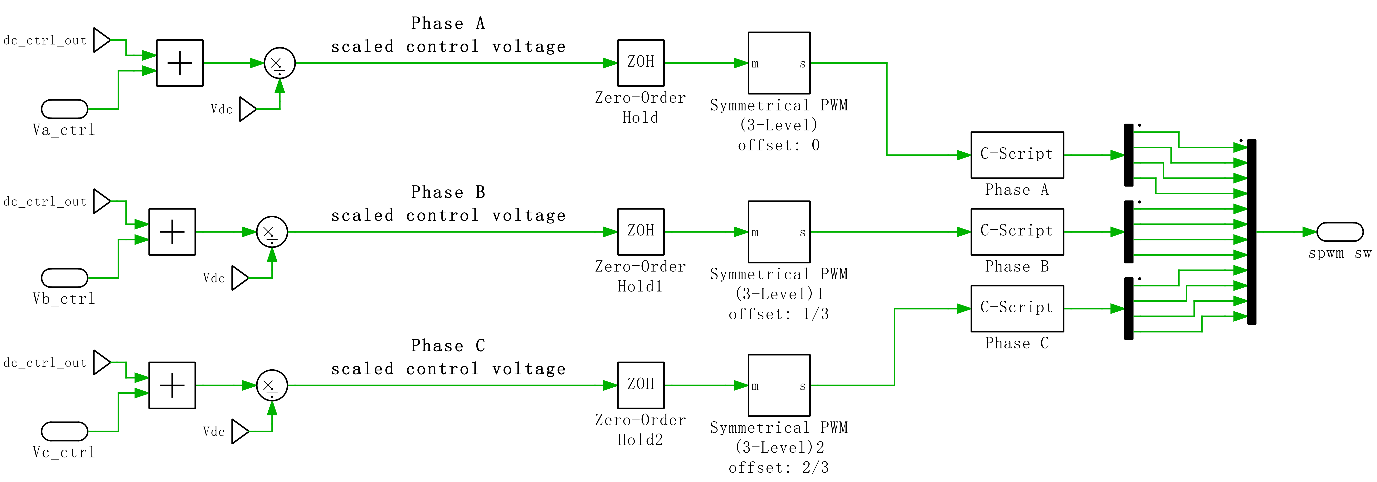
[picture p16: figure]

Figure 2.9 Three-Phase SPWM in Simulation

The sampling mode of the module is chosen to be “Natural (carrier starts with min)”, and negative carrier is set to be flipped rather than shifted. The carrier frequency is set to be 10 kHz (switching frequency). A “Zero-Order Hold” module is added to each phase to convert continuous control voltage to discrete. The “C-Script” after the “Symmetrical PWM (3-Level)” module is used to separate the output signal to PWMs of each gate. The waveform of the Symmetrical PWM (3-Level) module is presented in Figure 2.10.

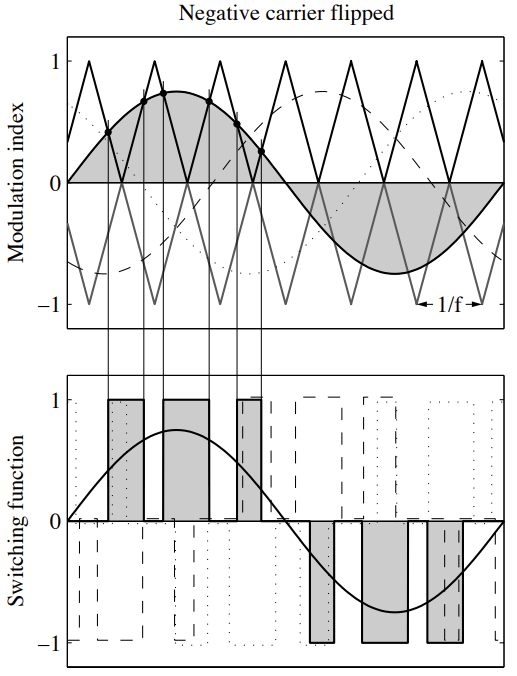
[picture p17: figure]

Figure 2.10 Symmetrical PWM (3-Level) Waveform

2.5.2 Space Vector PWM (SVPWM)

Another method to generate PWMs for each gate of inverter is Space Vector PWM (SVPWM). Compared to SPWM, the SVPWM is often favoured for its higher voltage utilization rate and lower THD (Total Harmonic Distortion) in the motor current (thus less noise and heat). It treats the three-phase voltages as a two-dimensional vector space, and utilizes the vector space of the inverter more efficiently by calculating the switching states that will produce the desired voltage vector closest to the ideal circular locus of the motor phase voltages. In this space, the possible voltage vectors that can be applied to the motor form a hexagon, which is shown in Figure 2.11 below.

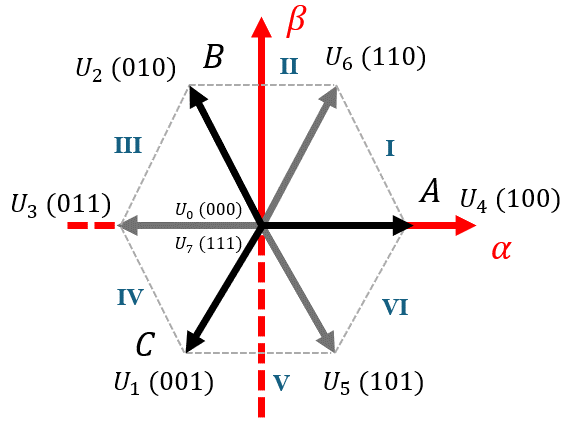
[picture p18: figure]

Figure 2.11 Frame of SVPWM (Not for Three-Level)

The left digit of the three-digits represents the status of phase A, the middle digit represents the status of phase B, and the right digit represents the status of phase C. U_3 , U_5 , U_6 are vectors synthesized from vectors in phase A, B, C. U_0 and U_7 represent zero vectors. These vectors divide the hexagon into six sectors (I to VI). The principle of SVPWM is to use these eight vectors (including two zero vectors) as base vectors to compound reference voltage vector.

According to the inductor volt-second balance principle, the average value of voltage applied across an ideal inductor must be zero. Therefore, the relationship between the reference voltage vector and two adjacent voltage vectors ( U_x , U_y ) in each sector can be given as follows. For example, U_x =U_4 and U_y =U_6 in Sector I; U_x =U_6 and U_y =U_2 in Sector II, etc.

∫_0^T U_(ref) dt=∫_0^(T_x) U_x dt+∫_(T_x)^(T_x +T_y) U_y dt+∫_(T_x +T_y)^T U_0^(*) dt Eqn.2.28

After discretization, it is equivalent to the following equations:

U_(ref) ∙T=U_x ∙T_x +U_y ∙T_y +U_0^(*) ∙T_0^(*) Eqn.2.29

|U_x |=|U_y |=2/3U_(dc) Eqn.2.30

T_x +T_y +T_0^(*) =T Eqn.2.31

The symbol T represents one period of PWM, which is 0.1 ms in this case. The symbol U_0^(*) represents the two zero vectors, which could be U_0 or U_7 . Proper placement of zero vectors can make the switching of the space voltage vector smoother. Duty cycles of U_x , U_y , U_0^(*) could be given by dividing their conducting time ( T_x , T_y , T_0^(*) ) by T , and they would be denoted as D_x , D_y , D_0^(*) in the following:

D_x =√3∙(|U_(ref) |)/(U_(dc))∙sin(N_(sec) ∙π/3-θ_e ) Eqn.2.32

D_y =√3∙(|U_(ref) |)/(U_(dc))∙sin(θ_e -(N_(sec) -1)∙π/3) Eqn.2.33

D_0^(*) =1-D_x -D_y Eqn.2.34

The symbol N_(sec) represents the sector number. Then, the three-phase voltage U_a , U_b , U_c could be expressed by D_x , D_y , D_0^(*) . To have symmetrical PWM, the distribution of zero vector to U_0 and U_7 can be given by:

T_0 =T_7 =1/2T_0^(*) ⇒ D_0 =D_7 =1/2D_0^(*) Eqn.2.35

The next step is to design the sequence of switching for three-phase. Due to the IGBTs have switching loss, it is essential to reduce the switching times of IGBT in sequence design. According to a method named “Seven-Segments SVPWM Sequence”, the sequence for each sector could be designed as shown in Table 2.3.

Table 2.3 Seven-Segment SVPWM Sequence

Sector | Sequence
I | 0-4-6-7-7-6-4-0
II | 0-2-6-7-7-6-2-0
III | 0-2-3-7-7-3-2-0
IV | 0-1-3-7-7-3-1-0
V | 0-1-5-7-7-5-1-0
VI | 0-4-5-7-7-5-4-0

The above derivation demonstrates the working principles of SVPWM. However, it is only for the case when each phase of the inverter contains two switching devices, so there are only two status (0 and 1) in each phase. For three-level inverter, there are three status (-1, 0, 1) in each phase, and the sequence design would be more complex than Table 2.3. Considering the complexity of algorithm, a “Space Vector PWM” module is used in PLECS simulation, and the SVPWM is not considered in the deployment to MCU.

2.6 Design of Controllers

2.6.1 Schematic of Controllers in Simulation

The schematic of controllers is presented in Figure 2.12 below.

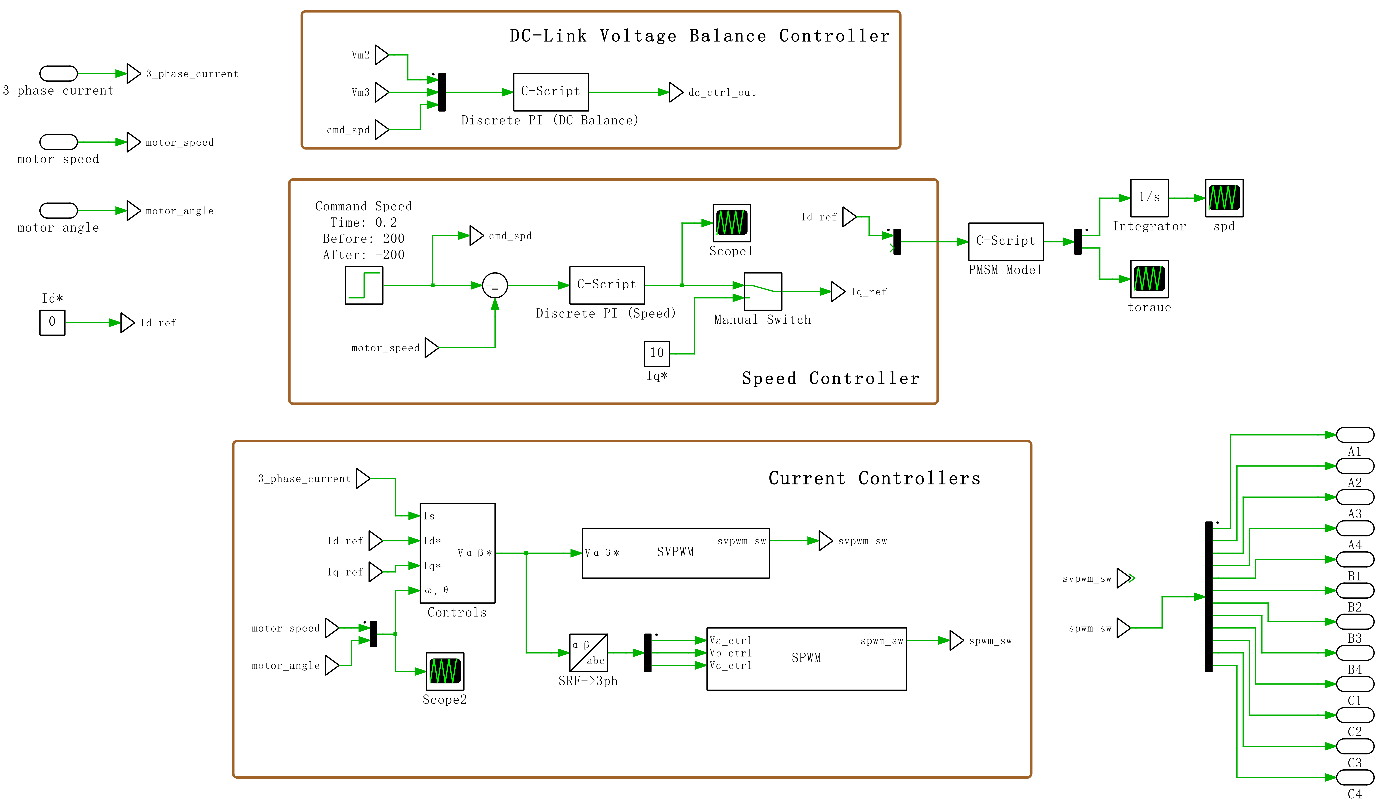
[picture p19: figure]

Figure 2.12 Schematic of Controllers in PLECS

According to the control diagram shown in Figure 2.8, the schematics of current controllers (sub-systems) are designed as follows (presented in Figure 2.13 and Figure 2.14 below).

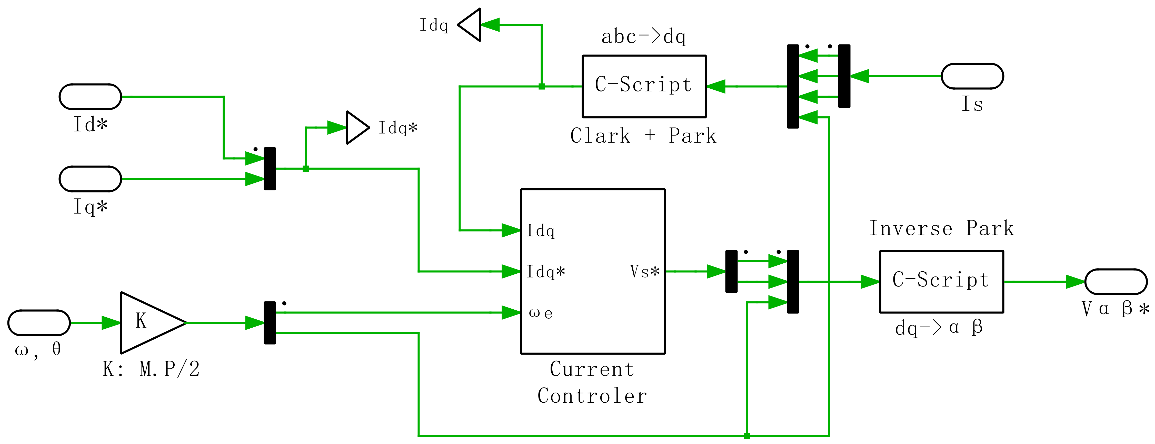
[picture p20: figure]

Figure 2.13 Current Controller Sub-System 1: Frame Transformation

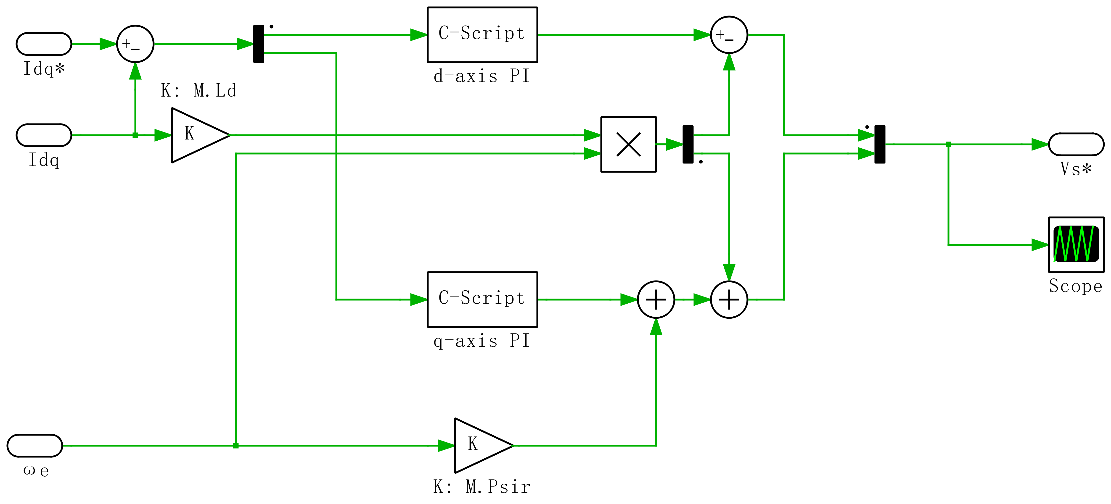
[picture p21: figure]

Figure 2.14 Current Controller Sub-System 2: PI Controllers

2.6.2 Current Controller

Continuous -> discrete

Time delay

Crossover frequency

Bandwidth / margin

Bode / root locus

According to the Eqn.2.5, the stator inductance of d-axis and q-axis are equal. Thus, the transfer function of plant (electrical system) should be identical, which can be expressed as:

P_e (s)=(i_d)/(V_d^(*))=(i_q)/(V_q^(*))=1/(R_s +sL_s) Eqn.2.36

2.6.3 Speed Controller

Electromotive force constant K_e

The motor torque and back emf constants are equal: K_e =K_t (represented by K)

Newton’s 2nd law:

Jθ+Bθ=Ki

Kirchhoff’s voltage law:

L_s (di)/(dt)+R_s i=V-Kθ

Laplace transform:

s(Js+B)θ(s)=KI(s)

(L_s s+R_s )I(s)=V(s)-Ksθ(s)

Thus, plant’s transfer function of current control:

(I(s))/(V(s))=1/((L_s s+R_s )+(K^2)/(Js+B))

Plant’s transfer function of speed control:

(θ(s))/(I(s))=K/(Js+B)

2.6.4 DC-Link Voltage Balance Controller

Chapter 3: Hardware Design: Diode Clamped Inverter

3.1 Schematic

Component selection

Why use DC/DC converter

The whole schematic of diode clamped inverter board is put in the Appendix.

The switching devices are chosen to be IGBT instead of MOSFET, because the

3.2 DC-Link Capacitance Calculations

But in fact, it is hard to satisfy high voltage and larger capacitance at same time

3.3 Loss Calculations

Thermal, switching, conducting

3.4 PCB Layout

Choose of vias size, copper thickness, track width -> calculation

3.5 Physical Product

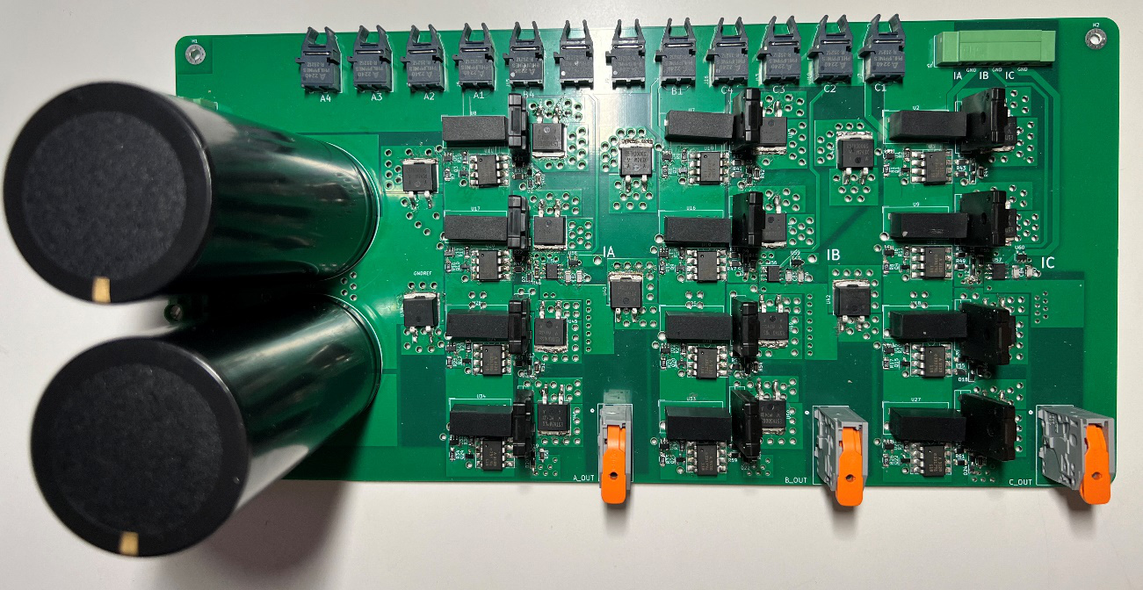
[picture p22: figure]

Chapter 4: Hardware Design: Control Board and its Peripherals

4.1 Schematic

4.2 PCB Layout

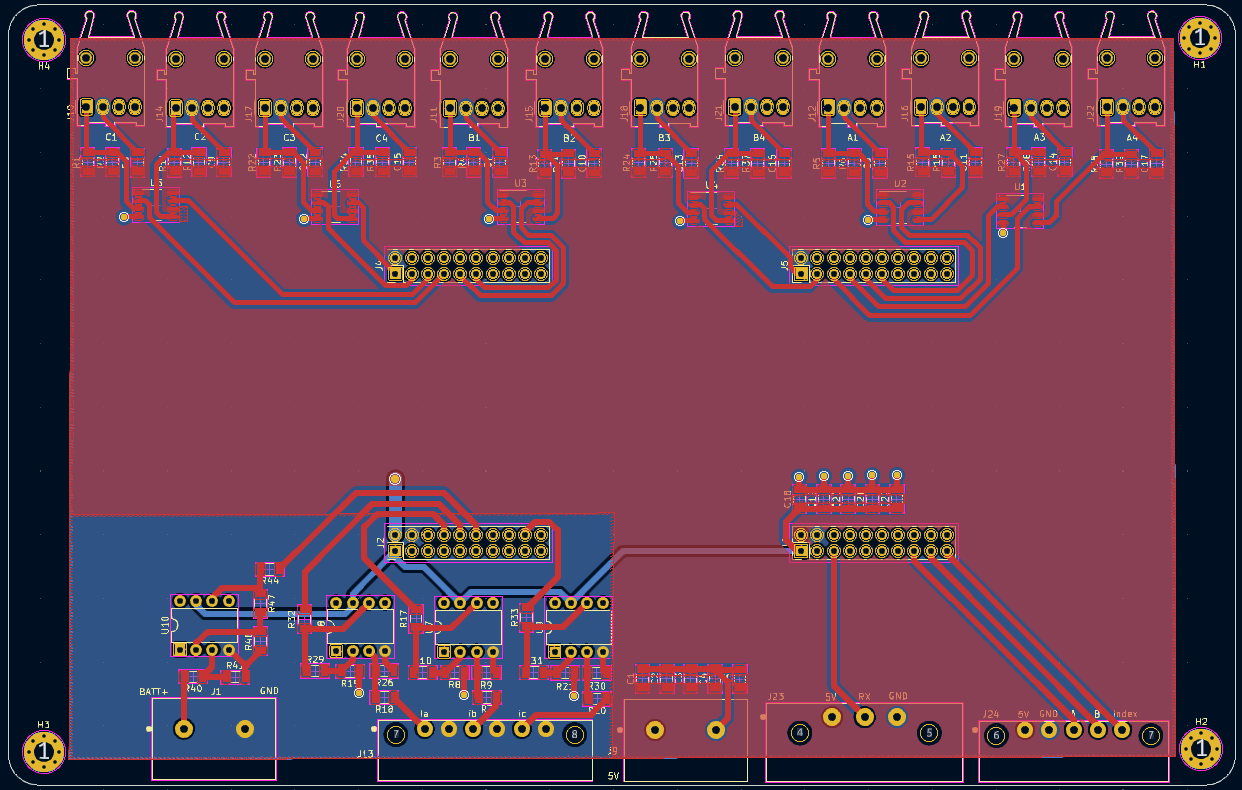
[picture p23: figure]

4.3 Physical Product

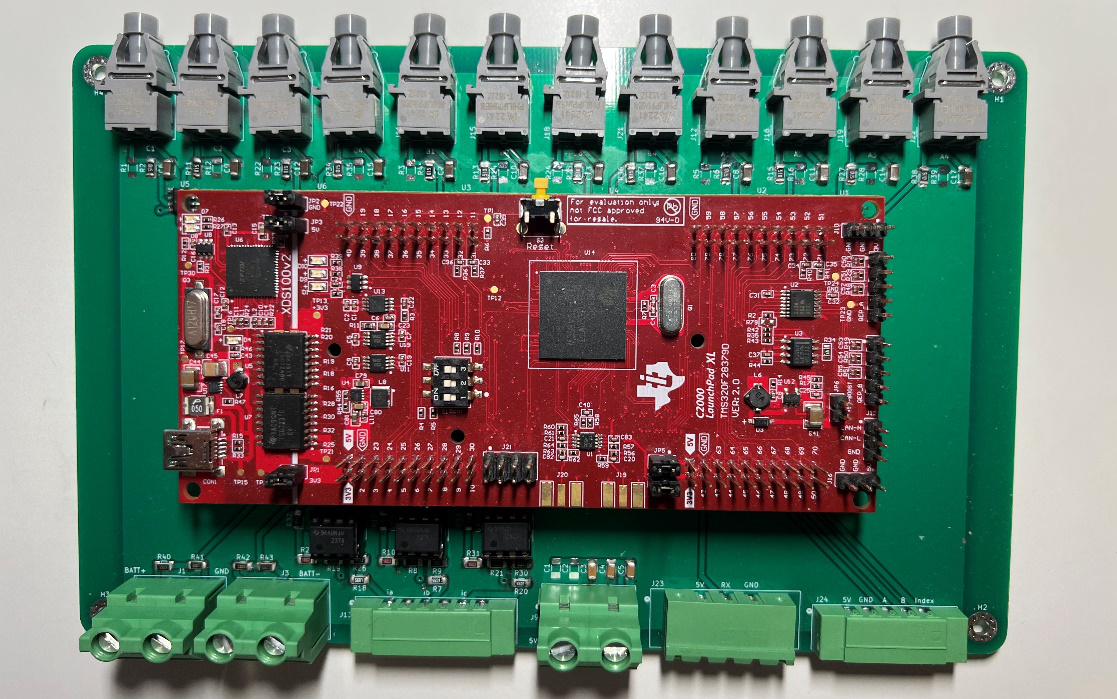
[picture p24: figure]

Chapter 5: Software Design: Implementation on MCU

5.1 Files Structure and IDE Configurations

Why choose CCS

5.2 Algorithm Implementation

5.2.1 ADC

5.2.2 SPWM

5.2.3 PI Controller

5.2.4 Control Logic

Chapter 6: System Testing, Validation, and Analysis

6.1 Testing and Validation

6.2 Results Analysis

Chapter 7: Conclusion and Reflection

7.1 Consideration of System within Wider Context

7.2 Reflection on Management

References

[1] B. Wu, “High Power Converters and AC Drives”, Wiley IEEE, 2nd Edition, 2016

[2] G. Abad, “Power Electronics and Electric Drives for Traction Applications”, Wiley, 2016

[3] A. Hughes “Electric Motors and Drives: Fundamentals, types, and applications”, 5th Edition, Elsevier, 2019

[4] S. N. Vukosavic, “Electrical Machines”, Springer, 2012

Appendix

Schematic of three-phase three-level diode clamped inverter in KiCad:


Schematic of control board in KiCad:


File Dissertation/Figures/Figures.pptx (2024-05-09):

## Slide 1


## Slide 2

Voltage error between two DC-link capacitors

PI

+

+

V_q^(∗)

Inverse Park Transform

V_α^(∗)

V_β^(∗)

Inverse Clarke + SPWM
or
SVPWM

V_d^(∗)

PWMs

Diode Clamped Inverter

ω_m^(∗)

+

PI

I_q^(∗)

+

PI

ω_m

θ_e

I_q

I_d^(∗)

θ_e

I_d

+

PI

Park Transform

ω_m , θ_m

Clarke Transform

Speed / Mechanical Position Decoding

I_A

A

B

C

I_B

PMSM

ω_e , θ_e

Gain = Pole Pairs

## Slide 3

I_q^(∗)

+

PI

V_q^(∗)

Inverse Park Transform

V_α^(∗)

V_β^(∗)

Inverse Clarke + SPWM
or
SVPWM

I_q

I_d^(∗)

V_d^(∗)

PWMs

Diode Clamped Inverter

I_d

+

PI

θ_e

Park Transform

ω_m , θ_m

θ_e

Clarke Transform

Speed / Mechanical Position Decoding

I_A

I_B

A

B

C

Gain = Pole Pairs

PMSM

ω_e , θ_e

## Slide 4

ω_e ∙(I_d ∙L_s +φ_m^(′) )

Voltage error between two DC-link capacitors

PI

+

+

+

V_q^(∗)

Inverse Park Transform

V_α^(∗)

V_β^(∗)

Inverse Clarke + SPWM
or
SVPWM

V_d^(∗)

PWMs

Diode Clamped Inverter

ω_m^(∗)

+

PI

I_q^(∗)

+

PI

ω_m

I_q

ω_e ∙I_q ∙L_s

+

θ_e

I_d^(∗)

θ_e

I_d

+

PI

Park Transform

ω_m , θ_m

Clarke Transform

Speed / Mechanical Position Decoding

I_A

A

B

C

I_B

PMSM

ω_e , θ_e

Gain = Pole Pairs

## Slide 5

β

q

β

B

q

rotor

d

d

A

S

N

θ_e

α

stator

α

C

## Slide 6

β

U_2 (010)

U_0 (000)

B

II

U_6 (110)

VI

III

IV

C

U_1 (001)

I

U_3 (011)

V

U_5 (101)

A

U_4 (100)

U_7 (111)

α

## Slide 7

G_C (s)=(K_p (s+a))/s

G_F (s)=1/(R_s +sL_s)

I_(ref) (s)

+

e_I (s)

V_(INV) (s)

I_(AC) (s)

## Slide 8


User Created Lib

⇒

Library, Makefiles, etc.

Main (program runs here)

⇒

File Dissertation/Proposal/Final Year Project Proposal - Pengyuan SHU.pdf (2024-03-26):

## EEEE3001 / EEEE4008


## Final Year Individual Project Proposal

## Diode Clamped Converter for Vehicle AC machine Drive

AUTHOR: | Mr. Pengyuan Shu
ID NUMBER: | 20321149
SUPERVISOR: | Dr. Alan Watson
MODERATOR: | Dr. Gaurang Vakil
DATE: | 25 October 2023

## Project files and overall progress are available at: https://github.com/ssyps2/PMSM_Motor_FOC

# 1. Overview

## 1.1 Introduction

In the contemporary landscape characterized by a growing emphasis on clean and sustainable energy sources, the integration of battery-connected Permanent Magnet Synchronous Machine (PMSM) drives assumes a pivotal role across diverse applications, most notably in the domain of electric vehicles. These systems leverage the distinctive architecture of multilevel converters, enabling the generation of multi-level AC voltage waveforms sans the requirement of transformers. Diode Clamped Converter (DCC) is one of the types of multilevel topologies, which is commonly used as drives for high frequency motors as a result of their superior waveform quality [1]. This intrinsic characteristic empowers it to produce high-frequency AC voltages for the PMSM, characterized by notably diminished harmonic distortion. Consequently, the need for extensive filtering and the associated pulsations stemming from these harmonics is substantially reduced.

A fundamental aspect of the PMSM motor is its rotor, which comprises permanent magnets, thus obviating the need for magnetizing current. In this configuration, the motor's torque is solely generated by the stator current. Owing to this inherent efficiency, PMSM motors find widespread application in fields such as robotics and aerospace, where minimizing losses in the rotor is of paramount importance. The control of PMSM motors typically hinges on the Field Oriented Control (FOC) methodology, which can be used to control the AC quantities (voltage, current) [2, 3]. Against this backdrop, the primary focus of this project is to explore the integration of the Diode Clamped Converter into the PMSM drive [4]. For safety reasons, only low-power scenarios (2kW) will be considered. The potential ramifications of this endeavour extend to a wide array of domains, including electric vehicles, renewable energy systems, robotics, and beyond. The successful execution of this project bears the promise of delivering more efficient energy solutions, and in so doing, opens the door to fresh commercial opportunities and contributes to broader economic growth.

## 1.2 Aim

The aim of this project is to simulate a 3-Phase Diode Clamped Inverter as a battery connected Permanent Magnet Synchronous Machine (PMSM) drive, and design a PCB to implement a low power version of this type of converter. The control algorithm will be tested in PLECS and eventually implemented in the F28379D micro-controller. Torque and speed closed loop control of the PMSM motor will be included.

## 1.3 Objectives

A. Simulation
The main topology of the circuit for simulation in the PLECS is shown in Figure 1.


Figure 1. Main Topology for Simulation

B. PCB Design
The circuit designed in the simulation will be implemented in a 2-layer Printed Circuit Board (PCB), which is a medium used to integrate all the electrical components. Surface Mount Technology (SMT) will be applied for more compact layout, higher design flexibility, and reducing the noise interference. The microcontroller is selected to be TI’s LAUNCHXL-F28379D, which is a 32-bit MCU with frequency up to 200MHz and sufficient communication interface (like UART, CAN, I2C) and high-speed PWM channels. Also, current sensor will be used to detect the 3-phase current and sampled by ADC to complete the torque control loop.

# 2. Specification

## 2.1 Software

The controller takes the 3-phase current and PMSM motor’s angle and speed as input, and output the PWM for each IGBT in the diode clamped converter. The controller contains two closed loops in series: torque loop and speed loop. The most fundamental loop is torque loop, which also can be referred to as current loop, as the torque of the PMSM motor is proportional to its stator current. This is where the FOC algorithm can be applied, combined with the PI controller to control the three-phase current in a closed loop to generate target torque based on the mechanical position of the rotor. Building upon the foundation of torque closed loop, the speed loop can be implemented by using the serial PI controller.

## 2.2 Hardware

The specification for 3 phase PMSM motor would be like:

Power Rating | 2kW
Frequency Rating | 50Hz/60Hz
Supply Voltage | 300-320V

## 2.3 Criteria for Success

a. PCB has no significant heating and vibration noise during operation.
b. Clear and correct 3 phase waveforms of both simulation and practical testing results.
c. Torque and speed of PMSM motor can be fully controlled by Qt-based HMI.

# 3. Methodology

No. | Goals and Processes | Challenges
1 | Read related resources to get familiar with the diode clamped converters and PMSM drives. | NA
2 | [Hardware] Select components according to the requirements (manufacturers can be Mouser, RS, Farnell…). The process is basically applying filter to exclude most irrelevant options, and compare those roughly fitted, then choose and order the best fit one (cheap / low loss / high tolerant…). | Some components might be unavailable / too expensive / take too long to ship
3 | [Hardware] Draw schematics based on selected components in KiCad, assign footprints to each component, and draw footprints that cannot found in the library. | Techniques for voltage balance between capacitors should be considered to prevent distortion.

4 | [Hardware] Plan PCB layout in KiCad, draw traces (ensure they are wide enough to handle large current) to connect components. Send project files to PCB factory for manufacturing. | Applying the design principles to reduce noise (should or should not use vias; thermal management on board; how to avoid ground bounce…)
5 | [Software] Whilst PCB is being manufactured, construct the diode clamped converter and the PMSM model in PLECS (fill up the parameters of PMSM simulation model according to the real machine model). | Mathematic modelling might be hard to implement; PMSM simulation model may not fit the real machine model well.
6 | [Software] Simulate the FOC algorithm and close the torque control loop in PLECS. Adjust the parameters to get expected output. | Implementation of FOC; Parameters of discrete PI controller might be difficult to tune.
7 | [Software] Further accomplish the speed closed loop control in PLECS. Adjust the parameters to get expected output. | Parameters tuning of discrete serial PI controller.
8 | [Hardware] Solder all the components to complete the converter construction, and test it with DC power source. | Small surface mount package components might be hard to solder on pads.
9 | [Software] Use Code Composer Studio (CCS) and Digital Power SDK to construct the embedded C code to implement the control algorithm on MCU, and validate simulation work with PCB connected to an RL load. | Task frequency will affect the parameters of PI controllers.
10 | Stretch target 1: Use the PCB to drive a low power PMSM motor with full FOC. | Realistic constrains of PMSM motor; Motor’s feedback data need to be logged and plotted.
11 | Stretch target 2: Design a Qt based human-machine interface (HMI) with a joystick for sending control commands to achieve torque and speed control of PMSM motor on a PC. | Delay might be occurred in data transmission, which will have negative impact on control.

# 4. Time Plan


# 5. Reference

[1] B. Wu, “High Power Converters and AC Drives”, Wiley IEEE, 2nd Edition, 2016
[2] G. Abad, “Power Electronics and Electric Drives for Traction Applications”, Wiley, 2016
[3] A. Hughes “Electric Motors and Drives: Fundamentals, types, and applications”, 5th Edition, Elsevier, 2019
[4] S. N. Vukosavic, “Electrical Machines”, Springer, 2012

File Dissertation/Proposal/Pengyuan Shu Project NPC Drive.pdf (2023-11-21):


Department of Electrical and Electronic Engineering

### Final Project Outline:

### Diode Clamped Converter for Vehicle AC machine Drive

Student: | Pengyuan Shu
Supervisor: | Dr. Alan Watson
Email | alan.watson@nottingham.ac.uk
Floor/Room: | B27, PEMC Building, Jubilee Campus
Telephone | 84462
Meetings: | In person on UP campus or over MS Teams

Aim

To simulate a Diode Clamped Converter (DCC) as a battery connected permanent magnet Synchronous machine (PMSM) drive and prove control operation using a designed PCB and experimental machine/RL load.

Introduction
Diode clamped converters (figure 1) are commonly used as drives for high frequency motors as a result of their superior waveform quality [1]. This enables the production of high frequency AC voltages for the machine with lower harmonic distortion, thus minimising filter requirements and pulsations caused by these harmonics. This project will consider their use as part of a simulation PMSM motor drive [2]. Furthermore, a PCB will be developed and sent for production which will implement a low power version of this type of converter which will be experimentally tested.


Figure 1: 3 Phase Diode Clamped Converter with split load

Control will be implemented using a F28379D micro-controller and therefore the C language based control will first be tested using the C-Script functionality in PLECS. The use of Field Oriented Control will provide a method of controlling the AC quantities (voltage, current) for this converter but using controller structures more commonly applied to DC systems such as PI controllers, simplifying design [3,4].

Tasks

The following broadly defined tasks should be arranged into a work plan. These tasks are not necessarily consecutive and are by no means exhaustive but should give the general framework of the project.

1. Familiarisation with Diode Clamped Converters and PMSM drives.
2. Development of a PCB, early in project, for implementing a low power (2kW) DCC.
3. Whilst PCB is being manufactured/populated implement in PLECS a DCC and PMSM drive with control.
4. Complete construction of converter and implementation of control on microcontroller to validate simulation work with the converter connected to an RL load.
5. Stretch target: Use PCB based DCC to drive a low power machine with full FOC.

References and Background Reading

Papers about DCC based drives and their control can be found via a combination of the internet, IEEEXplore, IET and the library. The following references will provide a solid foundation for this work.

[1] B. Wu, “High Power Converters and AC Drives”, Wiley IEEE, 2

nd Edition, 2016

[2] A. Hughes “Electric Motors and Drives: Fundamentals, types, and applications”, 5

th Edition, Elsevier, 2019

[3] S. N. Vukosavic, “Electrical Machines”, Springer, 2012
[4] G. Abad, “Power Electronics and Electric Drives for Traction Applications”, Wiley, 2016

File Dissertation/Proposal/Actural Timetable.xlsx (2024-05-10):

Stage | Number | Task | Weeks
 |  |  | 3 | 4 | 5 | 6 | 7 | 8 | 9 | 10 | 11 | 12 | 13 | 14 | 15 | 16 | 17 | 18 | 19 | 20 | 21 | 22 | 23 | 24 | 25 | 26 | 27 | 28 | 29 | 30 | 31 | 32 | 33 | 34 | 35 | 36 | 37
PCB Design | 1 | Read related resources to get familiar with the diode clamped converters and PMSM drives. |  |  |  |  |  |  |  |  |  | Revision and Prepare for Exam |  |  |  |  | Exam |  |  |  |  |  |  |  |  |  |  |  |  | Revision and Prepare for Exam |  |  |  |  | Exam and Presentation
 | 2 | Components selection according to the requirements, and order the components.
 | 3 | Draw the circuit schematic in KiCad.
 | 4 | Plan PCB layout in KiCad, send project files to PCB factory for manufacturing.
Simulation | 5 | Whilst PCB is being manufactured, construct the diode clamped converter and the PMSM model.
 | 6 | Simulate the FOC algorithm and close the torque control loop.
 | 7 | Further accomplish the speed closed loop control in PLECS
Overall Testing | 8 | Solder and test the quality of the two PCBs.
 | 9 | Construct the embedded C code in MCU.
 | 10 | Use the PCB to drive a low power PMSM motor with full FOC.
Thesis Writing
Prepare for Presentation

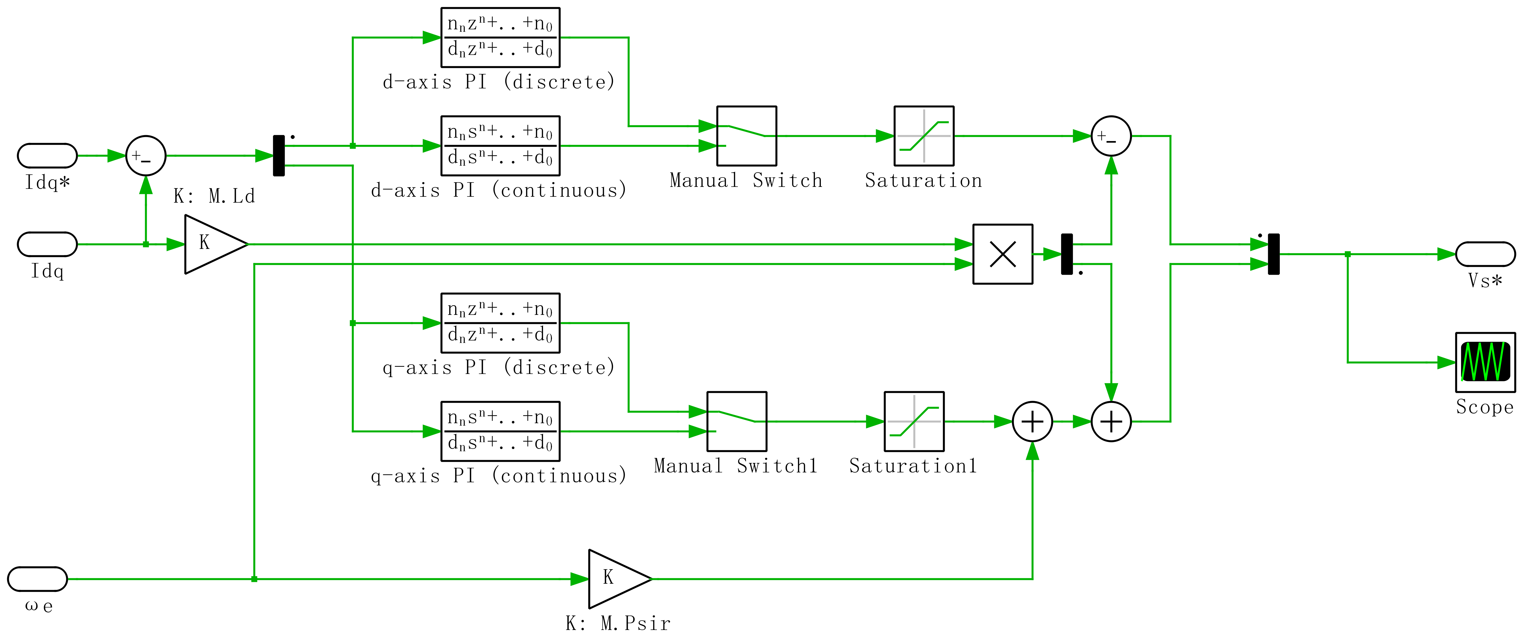
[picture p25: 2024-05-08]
Dissertation/Figures/current controller schematic 2.png

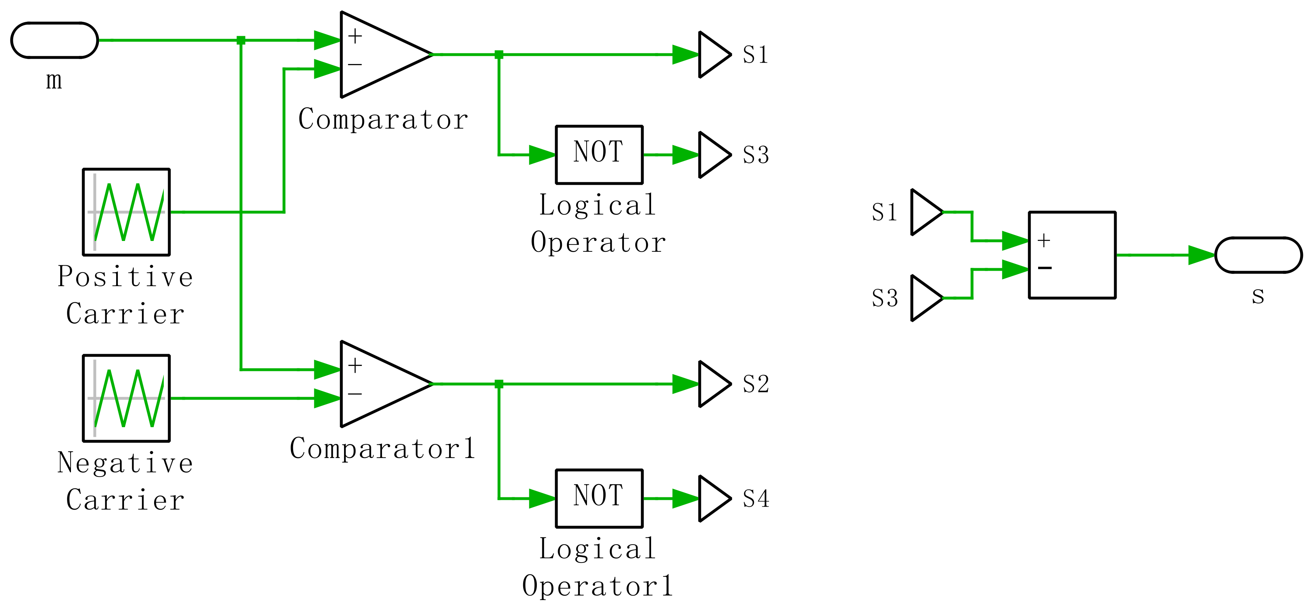
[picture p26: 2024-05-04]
Dissertation/Figures/symmetrical PWM schematic.png

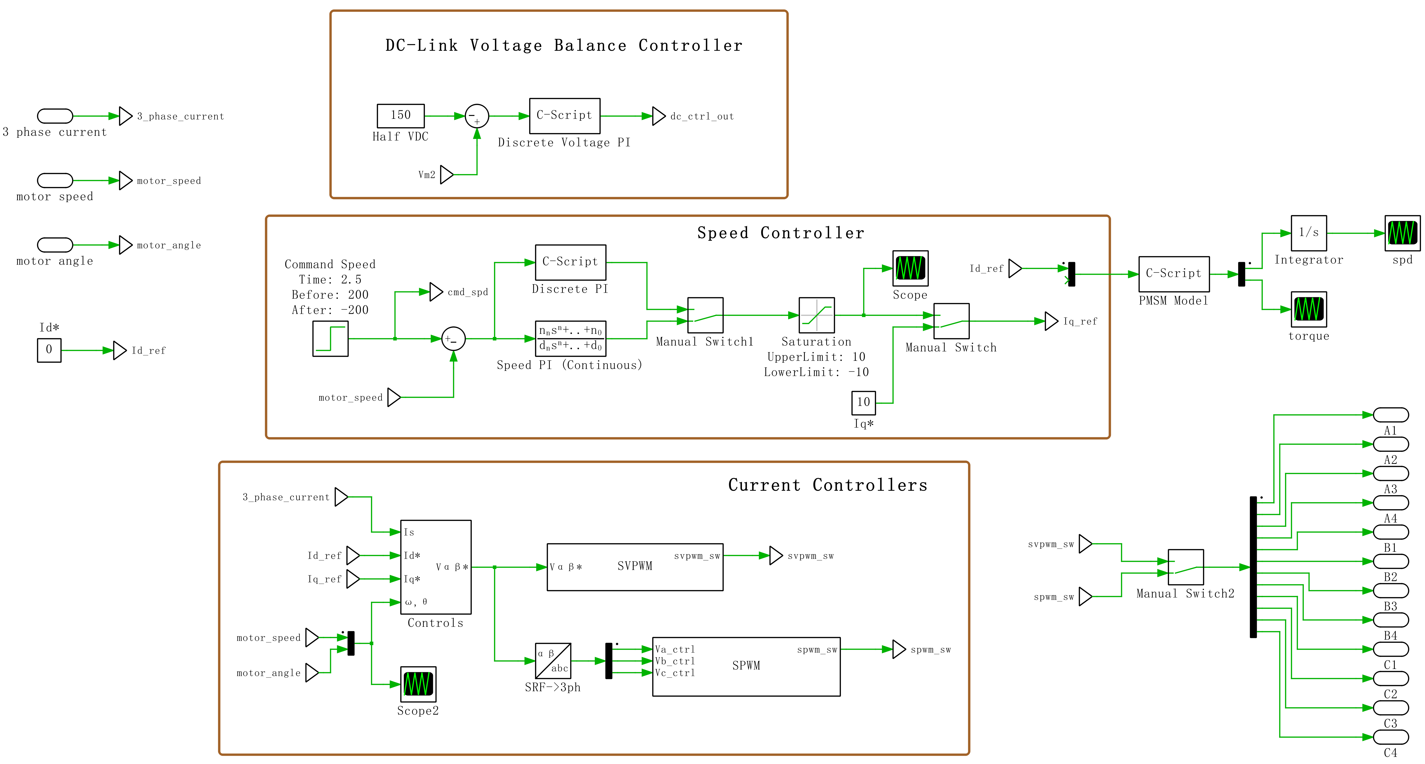
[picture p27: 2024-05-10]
Dissertation/Figures/controller schematic.png

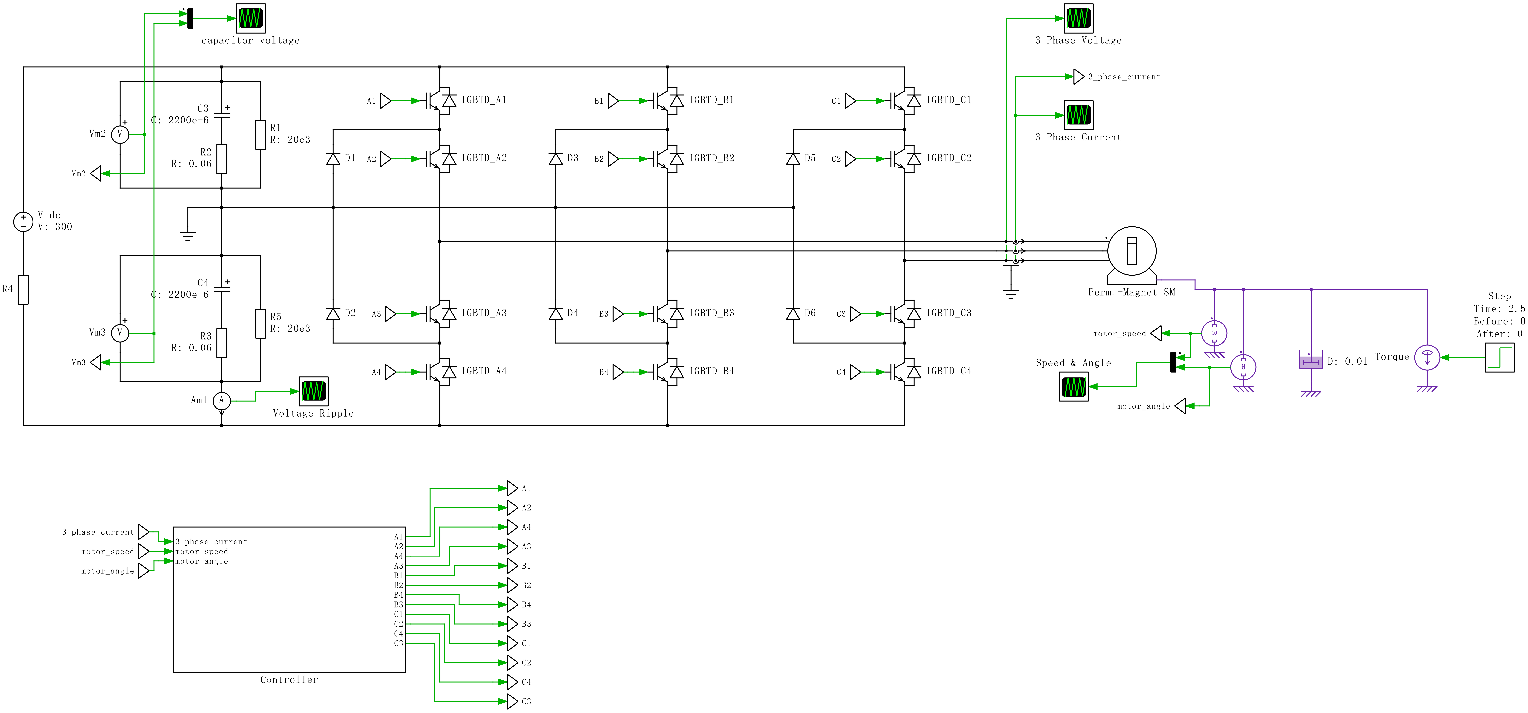
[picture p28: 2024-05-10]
Dissertation/Figures/simulation schematic.png

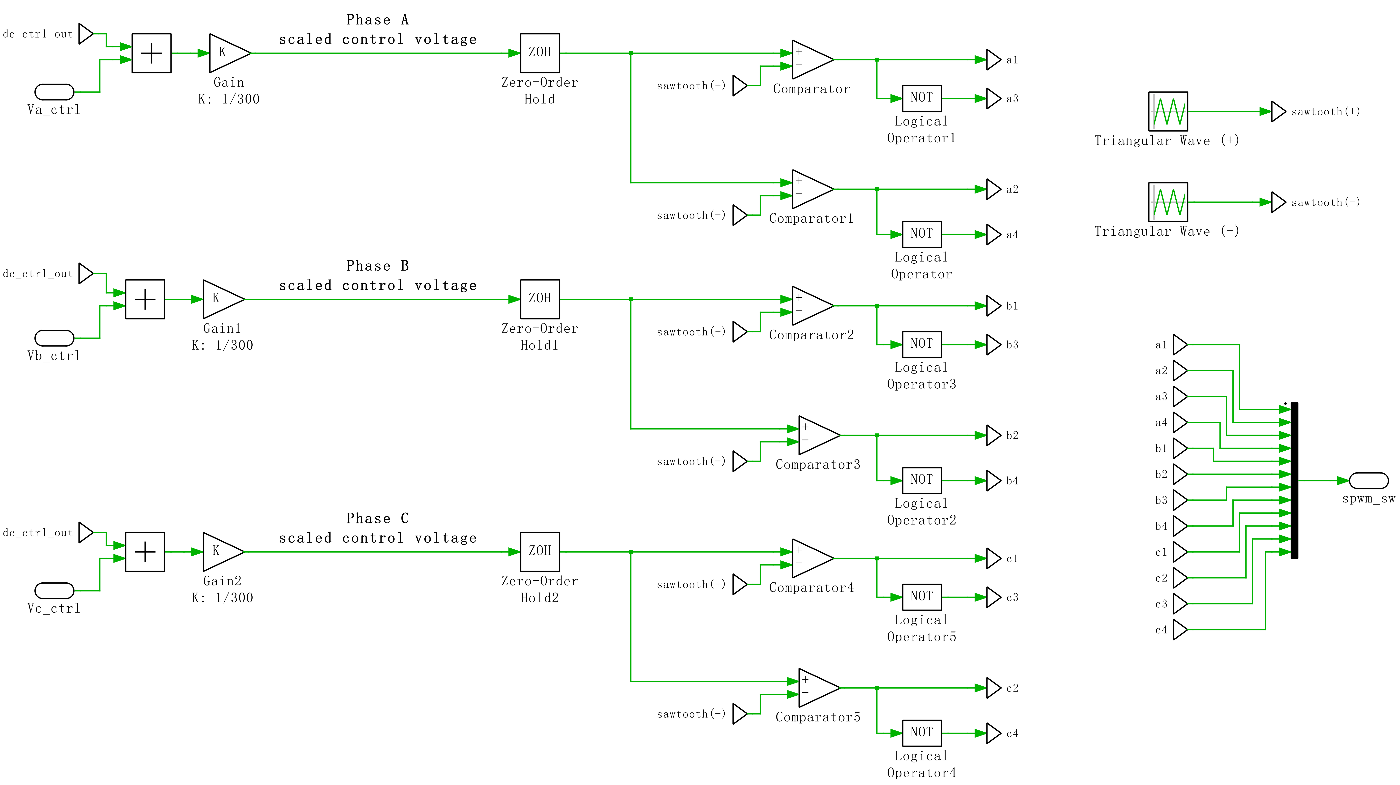
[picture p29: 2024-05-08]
Dissertation/Figures/SPWM schematic.png

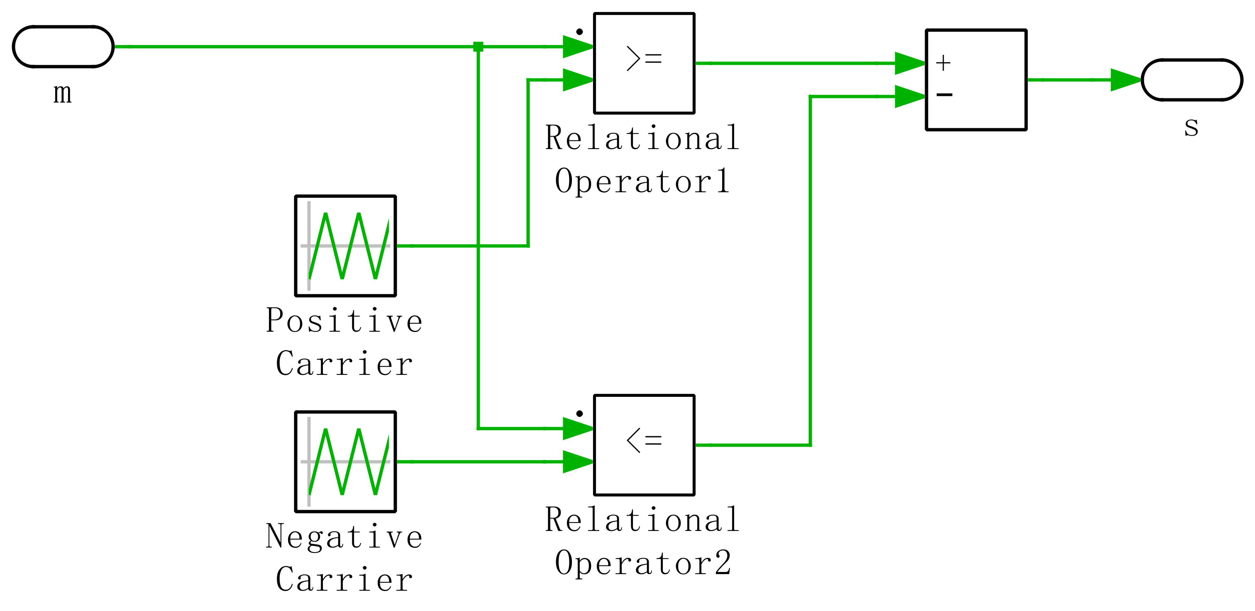
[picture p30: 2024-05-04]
Dissertation/Figures/schematic.png

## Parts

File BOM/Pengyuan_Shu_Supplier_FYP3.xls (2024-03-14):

 | The University of Nottingham |  | Purchase Requisition |  |  |  |  | FACULTY OF ENGINEERING
 | This is not an Official Order and should not be sent outside of the Faculty of Engineering
Suggested Supplier : |  | Mouser |  | Delivery Address
Address |  |  |  | ENG- Arch/Built Environment |  |  | ENG - ETC |  |  | Order No. Issued by Agresso
 |  |  |  | ENG- L2 Stores |  | X | ENG - NTEC
 |  |  |  | Eng - L3 Labs A06 |  |  | ENG - Manufacturing Labs
Tel/Fax Number |  |  |  | ENG-Building L4 |  |  | ENG - NGB
Quote/Contract Ref. |  |  |  | Elec Eng-Tower Building |  |  | ENG - Wolfson Building |  |  | Sciquest reference
Delivery Date Required: |  |  |  |  |  |  | BIO2 - Biology
 |  | (Important :Delivery Date must be a date. Do not use " ASAP" )
pos | Product Code (if known) | Description of Material / Service | Unit of Purchase | Quantity | Unit Price ex VAT £ |  | Line Value ex VAT £ | VAT % | VAT £ | Project Code | Activity Code | Safety Data Y/N
1 | 80-C1206C102K2G | C1206C102K2GACTU, 1n capacitor (SMD: 1206) | Each | 10 | 0.097 |  | £0.97 | 20.0 | £0.19
2 | 80-C1206C104J5R | C1206C104J5RACTU, 0.1u capacitor (SMD: 1206) | Each | 20 | 0.072 |  | £1.44 | 20.0 | £0.29
3 | 80-C1206C105K5RECAUT | C1206C105K5RECAUTO, 1u capacitor (SMD: 1206) | Each | 100 | 0.13 |  | £13.00 | 20.0 | £2.60
4 | 81-GRM31CR71H475KA2L | GRM31CR71H475KA12L, 4.7u capacitor (SMD: 1206) | Each | 20 | 0.207 |  | £4.14 | 20.0 | £0.83
5 | 81-GRM31CR71E106KA12 | GRM31CR71E106KA12L, 10u capacitor (SMD: 1206) | Each | 20 | 0.297 |  | £5.94 | 20.0 | £1.19
6 | 603-AC1206JR-0710RL | AC1206JR-0710RL, 10 ohm resistor (SMD: 1206) | Each | 20 | 0.034 |  | £0.68 | 20.0 | £0.14
7 | 603-RC1206JR-0751RL | RC1206JR-0751RL, 51 ohm resistor (SMD: 1206) | Each | 50 | 0.018 |  | £0.90 | 20.0 | £0.18
8 | 71-RCA1206100RFKEA | RCA1206100RFKEA, 100 ohm resistor (SMD: 1206) | Each | 30 | 0.053 |  | £1.59 | 20.0 | £0.32
9 | 603-RC1206FR-07270RL | RC1206FR-07270RL, 270 ohm resistor (SMD: 1206) | Each | 30 | 0.02 |  | £0.60 | 20.0 | £0.12
10 | 755-KTR18EZPF2002 | KTR18EZPF2002, 20k ohm resistor (SMD: 1206) | Each | 20 | 0.089 |  | £1.78 | 20.0 | £0.36
11 | 595-SN75451BD | SN75451BD, Transmitter Driver | Each | 12 | 0.593 |  | £7.12 | 20.0 | £1.42
12 | 80-ALC80C222FP400 | ALC80C222FP400, Electrolytic Capacitor, 2200 µF, 400 V, ± 20%, Snap-In, 9000 hours | Each | 2 | 23.13 |  | £46.26 | 20.0 | £9.25
13 | 595-SN74LVC04MDBVREP | SN74LVC1G04MDBVREP. Single invering buffer. SMD Package: SOT-23-5 | Each | 20 | 1.32 |  | £26.40 | 20.0 | £5.28
14 | 595-LMV641MF/NOPB | LMV641MF/NOPB. Operational Amplifier. SMD Package: SOT-23-5 | Each | 10 | 1.69 |  | £16.90 | 20.0 | £3.38
15 | 651-1714971 | 1714971. 600V 2 pin screw terminal | Each | 2 | 1.67 |  | £3.34 | 20.0 | £0.67
16 | 651-1827907 | 1827907. 6 Position Terminal Block Header | Each | 1 | 3.16 |  | £3.16 | 20.0 | £0.63
17 | 771-BC846B-T/R | BC846,215. NPN transistor. SMD Package: SOT-23 | Each | 20 | 0.065 |  | £1.30 | 20.0 | £0.26
18 |  | Delivery charge |  |  |  | £0.00 | £0.00 | 20.0 | £0.00
 |  |  |  |  | Total Order Value |  | £135.52 |  | £27.10 | £162.62
Requested by : |  | Pengyuan Shu | 23/02/2024 |  | Quotation Record
 |  | (Signature) (Print Name) | (Date) |  | Suppliers Name |  |  | Quote Ref. |  | Quote Value | Accepted / Rejected
Budget Holder |  | Mark Birkin
 |  | (Signature) (Print Name) | (Date)
Confirmation email to |  | ssyps2@nottingham.ac.uk
 | Please print | (email) (End user ) (Location)
 |  | Student id (where appropriate) | 20321149
 | RETURN TO THE FACULTY OF ENGINEERING FINANCE OFFICE ON COMPLETION
 |  |  |  |  |  |  |  |  |  | CE10/99

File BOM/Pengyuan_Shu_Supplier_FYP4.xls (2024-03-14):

 | The University of Nottingham |  | Purchase Requisition |  |  |  |  | FACULTY OF ENGINEERING
 | This is not an Official Order and should not be sent outside of the Faculty of Engineering
Suggested Supplier : |  | Mouser |  | Delivery Address
Address |  |  |  | ENG- Arch/Built Environment |  |  | ENG - ETC |  |  | Order No. Issued by Agresso
 |  |  |  | ENG- L2 Stores |  | X | ENG - NTEC
 |  |  |  | Eng - L3 Labs A06 |  |  | ENG - Manufacturing Labs
Tel/Fax Number |  |  |  | ENG-Building L4 |  |  | ENG - NGB
Quote/Contract Ref. |  |  |  | Elec Eng-Tower Building |  |  | ENG - Wolfson Building |  |  | Sciquest reference
Delivery Date Required: |  |  |  |  |  |  | BIO2 - Biology
 |  | (Important :Delivery Date must be a date. Do not use " ASAP" )
pos | Product Code (if known) | Description of Material / Service | Unit of Purchase | Quantity | Unit Price ex VAT £ |  | Line Value ex VAT £ | VAT % | VAT £ | Project Code | Activity Code | Safety Data Y/N
1 | 667-ERA-8AEB432V | Thin Film Resistors - SMD 1206 4.3Kohm 0.1% 25ppm | Each | 10 | 0.3 |  | £3.00 | 20.0 | £0.60
2 | 667-ERJ-S08F5601V | Thick Film Resistors - SMD 1206 5.6Kohms 1% Anti-Sulfur | Each | 10 | 0.3 |  | £3.00 | 20.0 | £0.60
3 | 667-ERJ-U08F1002V | Thick Film Resistors - SMD 1206 1% 10Kohm Anti-Sulfur AEC-Q200 | Each | 10 | 0.21 |  | £2.10 | 20.0 | £0.42
4 | 71-CRCW1206330RFKEAC | Thick Film Resistors - SMD 1/4Watt 330ohms 1% Commercial Use | Each | 10 | 0.053 |  | £0.53 | 20.0 | £0.11
5 | 651-1776511 | 1776511 5.08mm Pitch 3 Way Pluggable Terminal Block, Header | Each | 2 | 2.05 |  | £4.10 | 20.0 | £0.82
6 | 651-1777992 | 1777992 5.08mm Pitch 3 Way Pluggable Terminal Block, Plug, Plug-In, Screw Termination | Each | 2 | 3.14 |  | £6.28 | 20.0 | £1.26
7 | 651-1827897 | 1827897 MC Series Straight PCB Header, 5 Contact(s), 5.08mm Pitch, 1 Row(s) | Each | 2 | 2.95 |  | £5.90 | 20.0 | £1.18
8 | 651-1827732 | 1827732 3.81mm Pitch 5 Way Pluggable Terminal Block, Plug, Cable Mount, Screw Termination | Each | 2 | 5.49 |  | £10.98 | 20.0 | £2.20
9 | 595-TLV2371IP | TLV2371IP Texas Instruments, Precision, Op Amp, RRIO, 3MHz 21 kHz, 2.7 → 16 V, 8-Pin | Each | 5 | 1.39 |  | £6.95 | 20.0 | £1.39
10 |  | Delivery charge |  |  |  | £0.00 | £0.00 | 20.0 | £0.00
 |  |  |  |  | Total Order Value |  | £42.84 |  | £8.57 | £51.41
Requested by : |  | Pengyuan Shu | 17/02/2024 |  | Quotation Record
 |  | (Signature) (Print Name) | (Date) |  | Suppliers Name |  |  | Quote Ref. |  | Quote Value | Accepted / Rejected
Budget Holder |  | Mark Birkin
 |  | (Signature) (Print Name) | (Date)
Confirmation email to |  | ssyps2@nottingham.ac.uk
 | Please print | (email) (End user ) (Location)
 |  | Student id (where appropriate) | 20321149
 | RETURN TO THE FACULTY OF ENGINEERING FINANCE OFFICE ON COMPLETION
 |  |  |  |  |  |  |  |  |  | CE10/99

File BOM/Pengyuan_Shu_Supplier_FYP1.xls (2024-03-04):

 | The University of Nottingham |  | Purchase Requisition |  |  |  |  | FACULTY OF ENGINEERING
 | This is not an Official Order and should not be sent outside of the Faculty of Engineering
Suggested Supplier : |  | Mouser |  | Delivery Address
Address |  |  |  | ENG- Arch/Built Environment |  |  | ENG - ETC |  |  | Order No. Issued by Agresso
 |  |  |  | ENG- L2 Stores |  | X | ENG - NTEC
 |  |  |  | Eng - L3 Labs A06 |  |  | ENG - Manufacturing Labs
Tel/Fax Number |  |  |  | ENG-Building L4 |  |  | ENG - NGB
Quote/Contract Ref. |  |  |  | Elec Eng-Tower Building |  |  | ENG - Wolfson Building |  |  | Sciquest reference
Delivery Date Required: |  |  |  |  |  |  | BIO2 - Biology
 |  | (Important :Delivery Date must be a date. Do not use " ASAP" )
pos | Product Code (if known) | Description of Material / Service | Unit of Purchase | Quantity | Unit Price ex VAT £ |  | Line Value ex VAT £ | VAT % | VAT £ | Project Code | Activity Code | Safety Data Y/N
1 | 755-RGCL60TK60GC11 | RGCL60TK60GC11. IGBT (600V 30A). THT Package: TO-3P-3_Vertical | Item | 15 | 3.75 |  | £56.25 | 20.0 | £11.25 | A145R1
2 | 78-VS-E5TH3006S2L-M3 | VS-E5TH3006S2L-M3. Diode. SMD Package: TO-263-2 | Item | 20 | 1.75 |  | £35.00 | 20.0 | £7.00
3 | 78-BZX384C18-G3-18 | BZX384C18-G3-18. 18V Zener Diode | Item | 30 | 0.22 |  | £6.60 | 20.0 | £1.32
4 | 595-SN74LVC04MDBVREP | SN74LVC1G04MDBVREP. Single invering buffer. SMD Package: SOT-23-5 | Item | 15 | 1.5 |  | £22.50 | 20.0 | £4.50
5 | 771-BC846215 | BC846,215. NPN transistor. SMD Package: SOT-23 | Item | 15 | 0.1 |  | £1.50 | 20.0 | £0.30
6 |  | Delivery charge |  |  |  | £0.00 | £0.00 | 20.0 | £0.00
 |  |  |  |  | Total Order Value |  | £121.85 |  | £24.37 | £146.22
Requested by : |  | Pengyuan Shu | 6/12/12023 |  | Quotation Record
 |  | (Signature) (Print Name) | (Date) |  | Suppliers Name |  |  | Quote Ref. |  | Quote Value | Accepted / Rejected
Budget Holder |  | Mark Birkin
 |  | (Signature) (Print Name) | (Date)
Confirmation email to |  | ssyps2@nottingham.ac.uk
 | Please print | (email) (End user ) (Location)
 |  | Student id (where appropriate) | 20321149
 | RETURN TO THE FACULTY OF ENGINEERING FINANCE OFFICE ON COMPLETION
 |  |  |  |  |  |  |  |  |  | CE10/99

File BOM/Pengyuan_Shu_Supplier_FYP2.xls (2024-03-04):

 | The University of Nottingham |  | Purchase Requisition |  |  |  |  | FACULTY OF ENGINEERING
 | This is not an Official Order and should not be sent outside of the Faculty of Engineering
Suggested Supplier : |  | Digikey |  | Delivery Address
Address |  |  |  | ENG- Arch/Built Environment |  |  | ENG - ETC |  |  | Order No. Issued by Agresso
 |  |  |  | ENG- L2 Stores |  | X | ENG - NTEC
 |  |  |  | Eng - L3 Labs A06 |  |  | ENG - Manufacturing Labs
Tel/Fax Number |  |  |  | ENG-Building L4 |  |  | ENG - NGB
Quote/Contract Ref. |  |  |  | Elec Eng-Tower Building |  |  | ENG - Wolfson Building |  |  | Sciquest reference
Delivery Date Required: |  |  |  |  |  |  | BIO2 - Biology
 |  | (Important :Delivery Date must be a date. Do not use " ASAP" )
pos | Product Code (if known) | Description of Material / Service | Unit of Purchase | Quantity | Unit Price ex VAT £ |  | Line Value ex VAT £ | VAT % | VAT £ | Project Code | Activity Code | Safety Data Y/N
1 | 516-1789-6-ND | HCPL-3120-500E. Isolated gate driver. SMD Package: DIP-8_W8.89mm_LongPads | Item | 15 | 2.66 |  | £39.90 | 20.0 | £7.98
2 | 296-48929-6-ND | LMV641MF/NOPB. Operational Amplifier. SMD Package: SOT-23-5 | Item | 5 | 1.96 |  | £9.80 | 20.0 | £1.96
3 | 2946-2606-1101-ND | 2606-1101. 600V 1 pin terminal | Item | 3 | 2.42 |  | £7.26 | 20.0 | £1.45
4 | 277-1271-ND | 1714971. 600V 2 pin screw terminal | Item | 3 | 1.39 |  | £4.17 | 20.0 | £0.83
5 | 277-5806-ND | 1827907. 6 Position Terminal Block Header | Item | 2 | 2.88 |  | £5.76 | 20.0 | £1.15
6 | 277-5718-ND | 1827745. 6 Position Terminal Block Plug | Item | 2 | 4.91 |  | £9.82 | 20.0 | £1.96
7 | 620-1646-6-ND | ACS723LLCTR-40AB-T. Current sensor. SMD Package: 8-SOIC (3.90mm Width) | Item | 5 | 4.8 |  | £24.00 | 20.0 | £4.80
8 |  | Delivery charge |  |  |  | £0.00 | £0.00 | 20.0 | £0.00
 |  |  |  |  | Total Order Value |  | £100.71 |  | £20.14 | £120.85
Requested by : |  | Pengyuan Shu | 6/12/12023 |  | Quotation Record
 |  | (Signature) (Print Name) | (Date) |  | Suppliers Name |  |  | Quote Ref. |  | Quote Value | Accepted / Rejected
Budget Holder |  | Mark Birkin
 |  | (Signature) (Print Name) | (Date)
Confirmation email to |  | ssyps2@nottingham.ac.uk
 | Please print | (email) (End user ) (Location)
 |  | Student id (where appropriate) | 20321149
 | RETURN TO THE FACULTY OF ENGINEERING FINANCE OFFICE ON COMPLETION
 |  |  |  |  |  |  |  |  |  | CE10/99

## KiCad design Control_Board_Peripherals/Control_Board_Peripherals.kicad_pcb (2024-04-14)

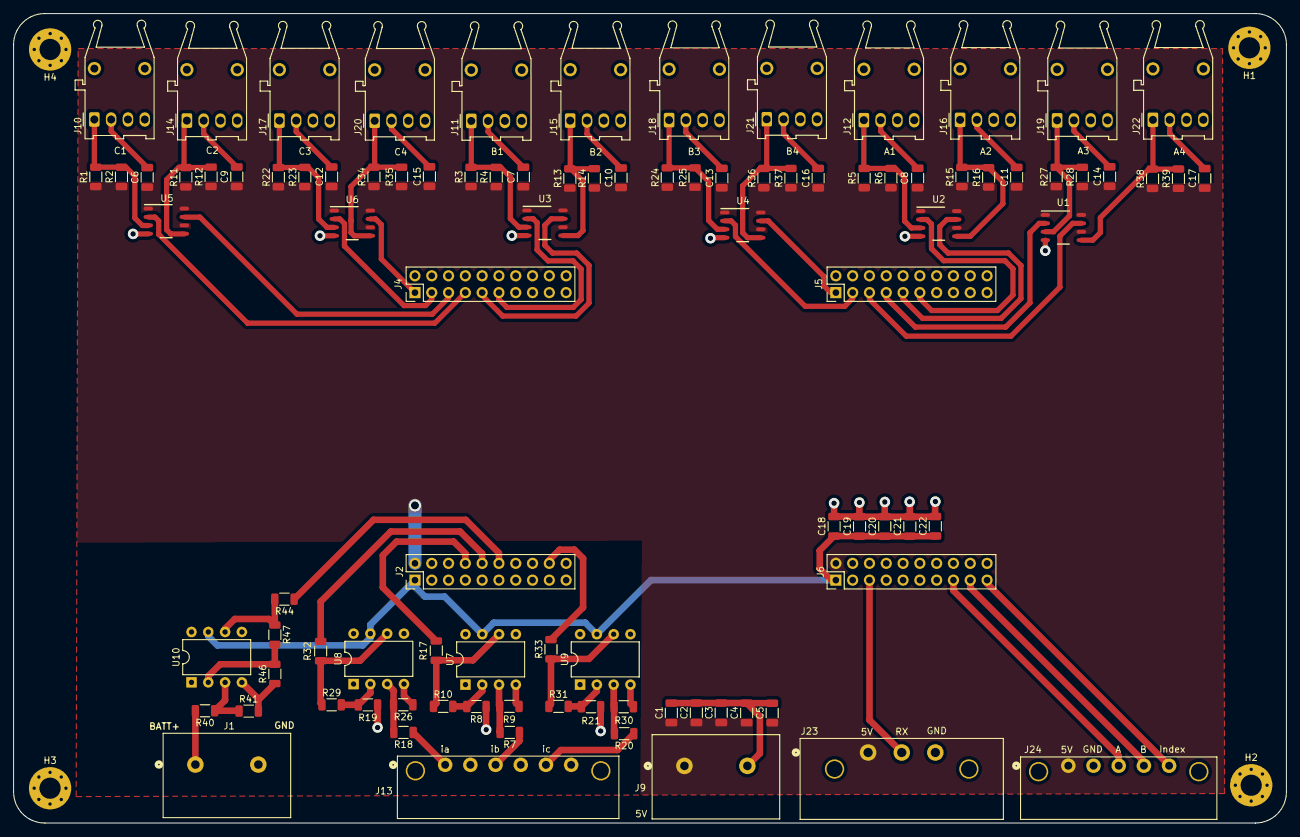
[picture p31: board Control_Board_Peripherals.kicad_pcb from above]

Board: 2 copper layers, 192.5 x 122.4 mm, 101 parts (0 on the bottom side), 51 nets.

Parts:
C1, C2, C3, C4, C5, C18, C19, C20, C21, C22: 0.1u; C_1206_3216Metric
C6, C7, C8, C9, C10, C11, C12, C13, C14, C15, C16, C17: 4.7u; C_1206_3216Metric
H1, H2, H3, H4: MountingHole; MountingHole_3.2mm_M3_Pad_Via
J1, J9: 1714971; CONN_1714971_PXC
J2, J4, J5, J6: Conn_02x10_Top_Bottom; PinHeader_2x10_P2.54mm_Vertical
J10, J11, J12, J14, J15, J16, J17, J18, J19, J20, J21, J22: HFBR-1521Z; Broadcom_AFBR-16xxZ_Horizontal
J13: 1827907; CONN_1827907
J23: Conn_01x03; CONN_1776511
J24: Conn_01x05; CONN_1827897
R1, R2, R3, R4, R5, R6, R11, R12, R13, R14, R15, R16, R22, R23, R24, R25, R27, R28, R34, R35, R36, R37, R38, R39: 100; R_1206_3216Metric
R7, R18, R20: 5.6k; R_1206_3216Metric
R8, R19, R21: 20k; R_1206_3216Metric
R9, R26, R30: 4.3k; R_1206_3216Metric
R10, R29, R31: 10k; R_1206_3216Metric
R17, R32, R33, R44: 330; R_1206_3216Metric
R40, R46: 100k; R_1206_3216Metric
R41, R47: 1k; R_1206_3216Metric
U1, U2, U3, U4, U5, U6: SN75451BD
U7, U8, U9, U10: TLV2371P; DIP-8_W7.62mm

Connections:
+3.3V: C18.1, C19.1, C20.1, C21.1, C22.1, J2.1, J6.41, U7.7 (V+), U8.7 (V+), U9.7 (V+), U10.7 (V+)
+BATT: J1.1, R40.2
/A1: J5.75, U2.2 (1B)
/A1_In: J12.1 (Data_In), R5.2, R6.2, U2.3 (1Y)
/A2: J5.76, U2.7 (2B)
/A2_In: J16.1 (Data_In), R15.2, R16.2, U2.5 (2Y)
/A3: J5.77, U1.2 (1B)
/A3_In: J19.1 (Data_In), R27.2, R28.2, U1.3 (1Y)
/A4: J5.78, U1.7 (2B)
/A4_In: J22.1 (Data_In), R38.2, R39.2, U1.5 (2Y)
/B1: J4.35 (Pin_5), U3.2 (1B)
/B1_In: J11.1 (Data_In), R3.2, R4.2, U3.3 (1Y)
/B2: J4.36, U3.7 (2B)
/B2_In: J15.1 (Data_In), R13.2, R14.2, U3.5 (2Y)
/B3: J5.79, U4.2 (1B)
/B3_In: J18.1 (Data_In), R24.2, R25.2, U4.3 (1Y)
/B4: J5.80, U4.7 (2B)
/B4_In: J21.1 (Data_In), R36.2, R37.2, U4.5 (2Y)
/C1: J4.37, U5.2 (1B)
/C1_In: J10.1 (Data_In), R1.2, R2.2, U5.3 (1Y)
/C2: J4.38, U5.7 (2B)
/C2_In: J14.1 (Data_In), R11.2, R12.2, U5.5 (2Y)
/C3: J4.39, U6.2 (1B)
/C3_In: J17.1 (Data_In), R22.2, R23.2, U6.3 (1Y)
/C4: J4.40, U6.7 (2B)
/C4_In: J20.1 (Data_In), R34.2, R35.2, U6.5 (2Y)
/CH_A: J6.48, J24.3
/CH_B: J6.49, J24.4
/Index: J6.50, J24.5
/SCIC_RX: J6.43, J23.2
/dc_sample: J2.26, R44.1
/ia_adc: J2.25, R32.1
/ib_adc: J2.24, R17.1
/ic_adc: J2.29, R33.1
GND: C1.2, C2.2, C3.2, C4.2, C5.2, C6.2, C7.2, C8.2, C9.2, C10.2, C11.2, C12.2, C13.2, C14.2, C15.2, C16.2, C17.2, C18.2, C19.2, C20.2, C21.2, C22.2, J1.2, J2.22, J4.20, J5.60, J6.62, J9.2, J10.2 (VEE), J11.2 (VEE), J12.2 (VEE), J13.2, J13.4, J13.6, J14.2 (VEE), J15.2 (VEE), J16.2 (VEE), J17.2 (VEE), J18.2 (VEE), J19.2 (VEE), J20.2 (VEE), J21.2 (VEE), J22.2 (VEE), J23.3, J24.2, R8.2, R9.2, R19.2, R21.2, R26.2, R30.2, R41.2, R46.1, U1.4 (GND), U2.4 (GND), U3.4 (GND), U4.4 (GND), U5.4 (GND), U6.4 (GND), U7.4 (V-), U8.4 (V-), U9.4 (V-), U10.4 (V-)
unnamed: R10.1, R17.2, U7.6
unnamed: R29.1, R32.2, U8.6
unnamed: R31.1, R33.2, U9.6
unnamed: R44.2, R47.1, U10.6
unnamed: R7.2, R9.1, U7.3 (+)
unnamed: R8.1, R10.2, U7.2 (-)
unnamed: R18.2, R26.1, U8.3 (+)
unnamed: R19.1, R29.2, U8.2 (-)
unnamed: R20.2, R30.1, U9.3 (+)
unnamed: R21.1, R31.2, U9.2 (-)
unnamed: R40.1, R41.1, U10.3 (+)
unnamed: R46.2, R47.2, U10.2 (-)
VCC: C1.1, C2.1, C3.1, C4.1, C5.1, C6.1, C7.1, C8.1, C9.1, C10.1, C11.1, C12.1, C13.1, C14.1, C15.1, C16.1, C17.1, J2.21, J6.61, J9.1, J23.1, J24.1, R1.1, R2.1, R3.1, R4.1, R5.1, R6.1, R11.1, R12.1, R13.1, R14.1, R15.1, R16.1, R22.1, R23.1, R24.1, R25.1, R27.1, R28.1, R34.1, R35.1, R36.1, R37.1, R38.1, R39.1, U1.1 (1A), U1.6 (2A), U1.8 (VCC), U2.1 (1A), U2.6 (2A), U2.8 (VCC), U3.1 (1A), U3.6 (2A), U3.8 (VCC), U4.1 (1A), U4.6 (2A), U4.8 (VCC), U5.1 (1A), U5.6 (2A), U5.8 (VCC), U6.1 (1A), U6.6 (2A), U6.8 (VCC)
ia_signal: J13.1, R18.1
ib_signal: J13.3, R7.1
ic_signal: J13.5, R20.1

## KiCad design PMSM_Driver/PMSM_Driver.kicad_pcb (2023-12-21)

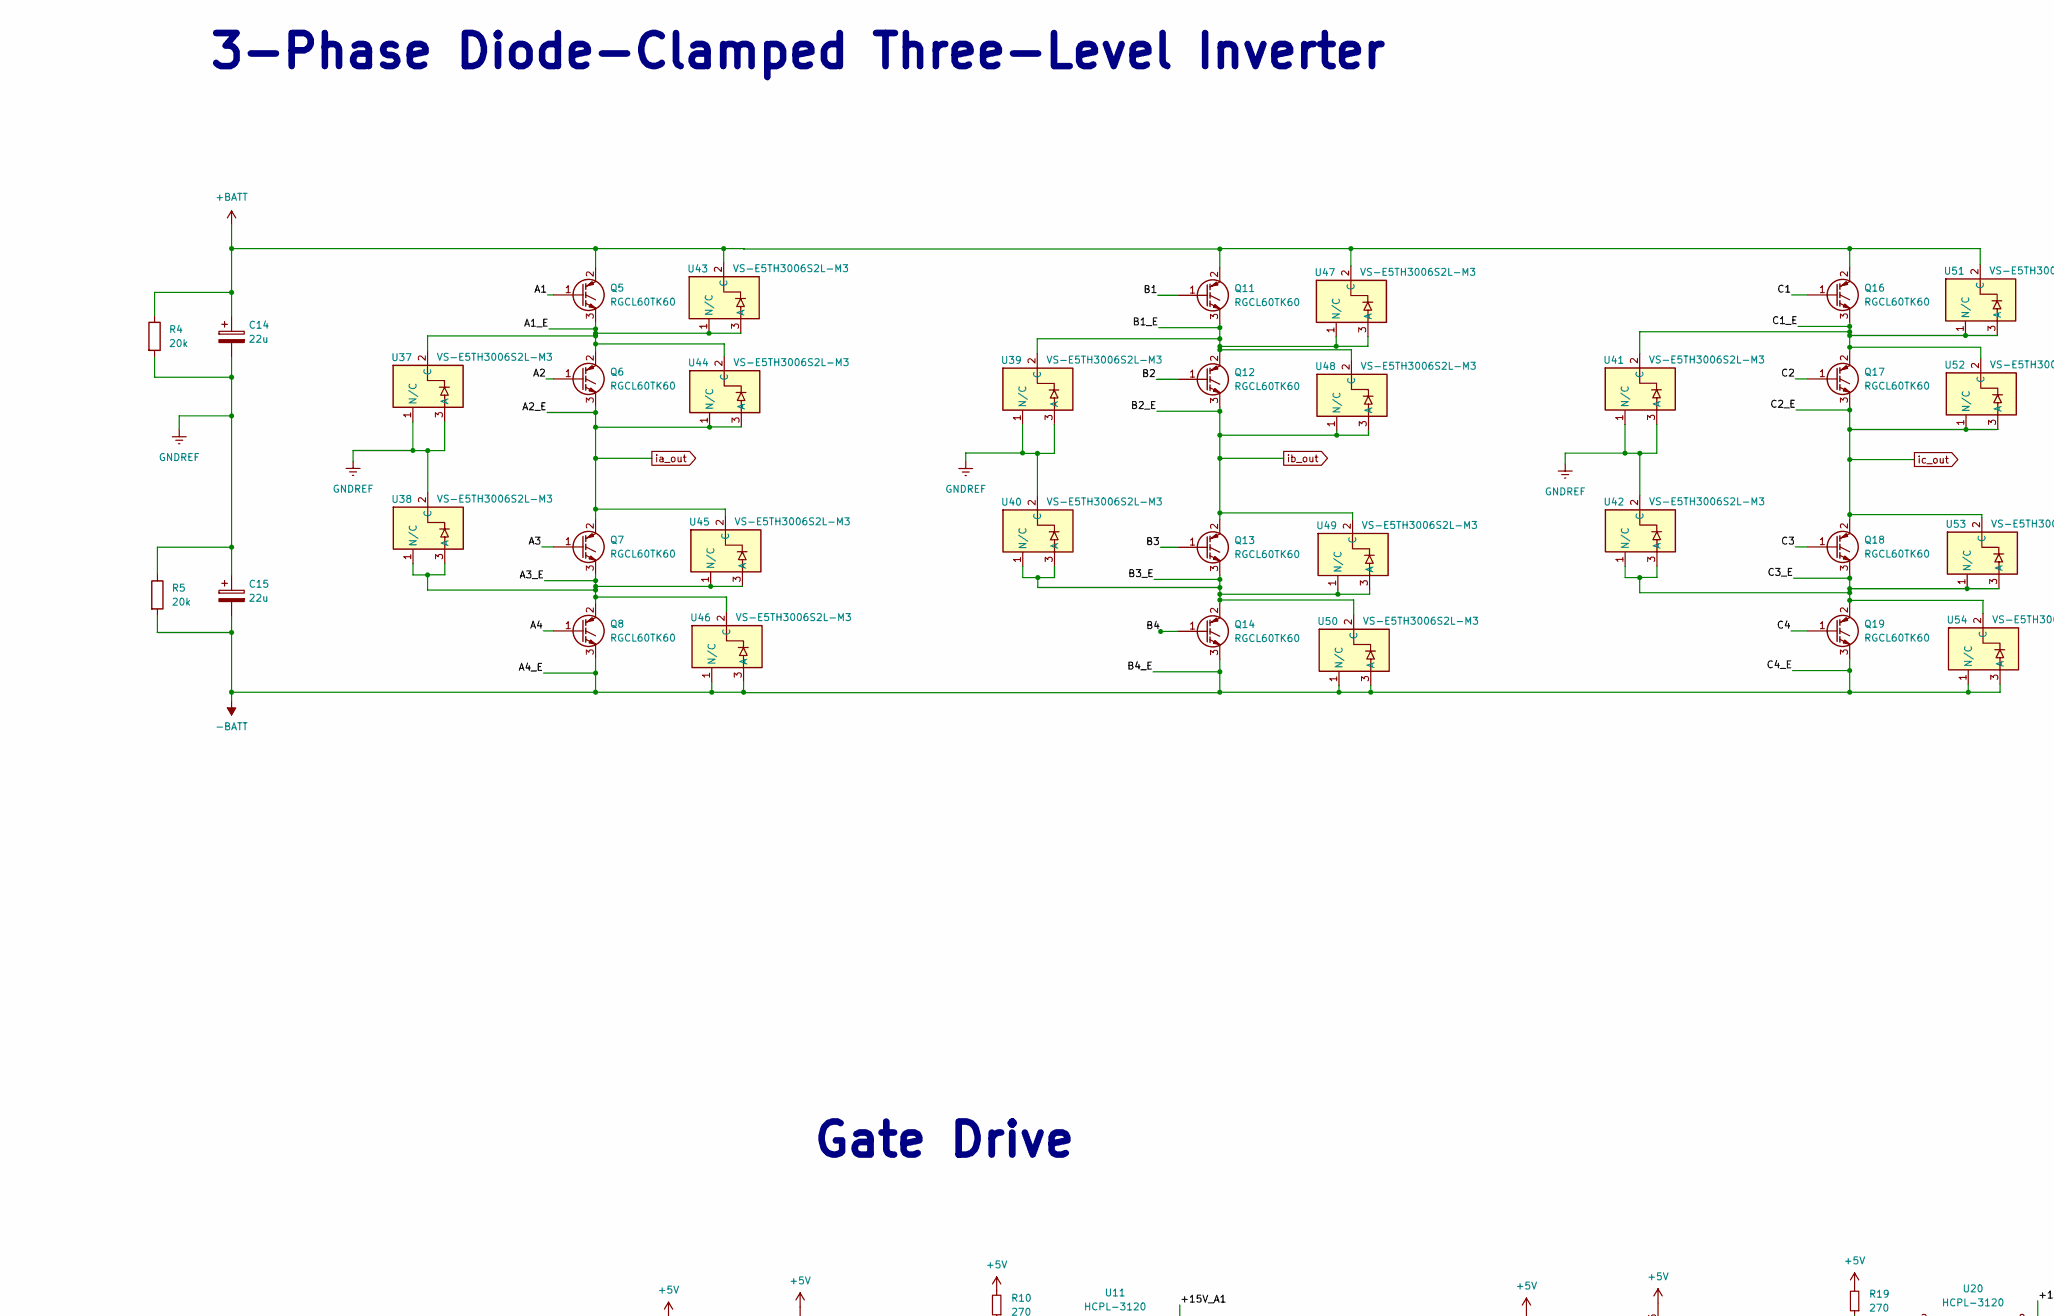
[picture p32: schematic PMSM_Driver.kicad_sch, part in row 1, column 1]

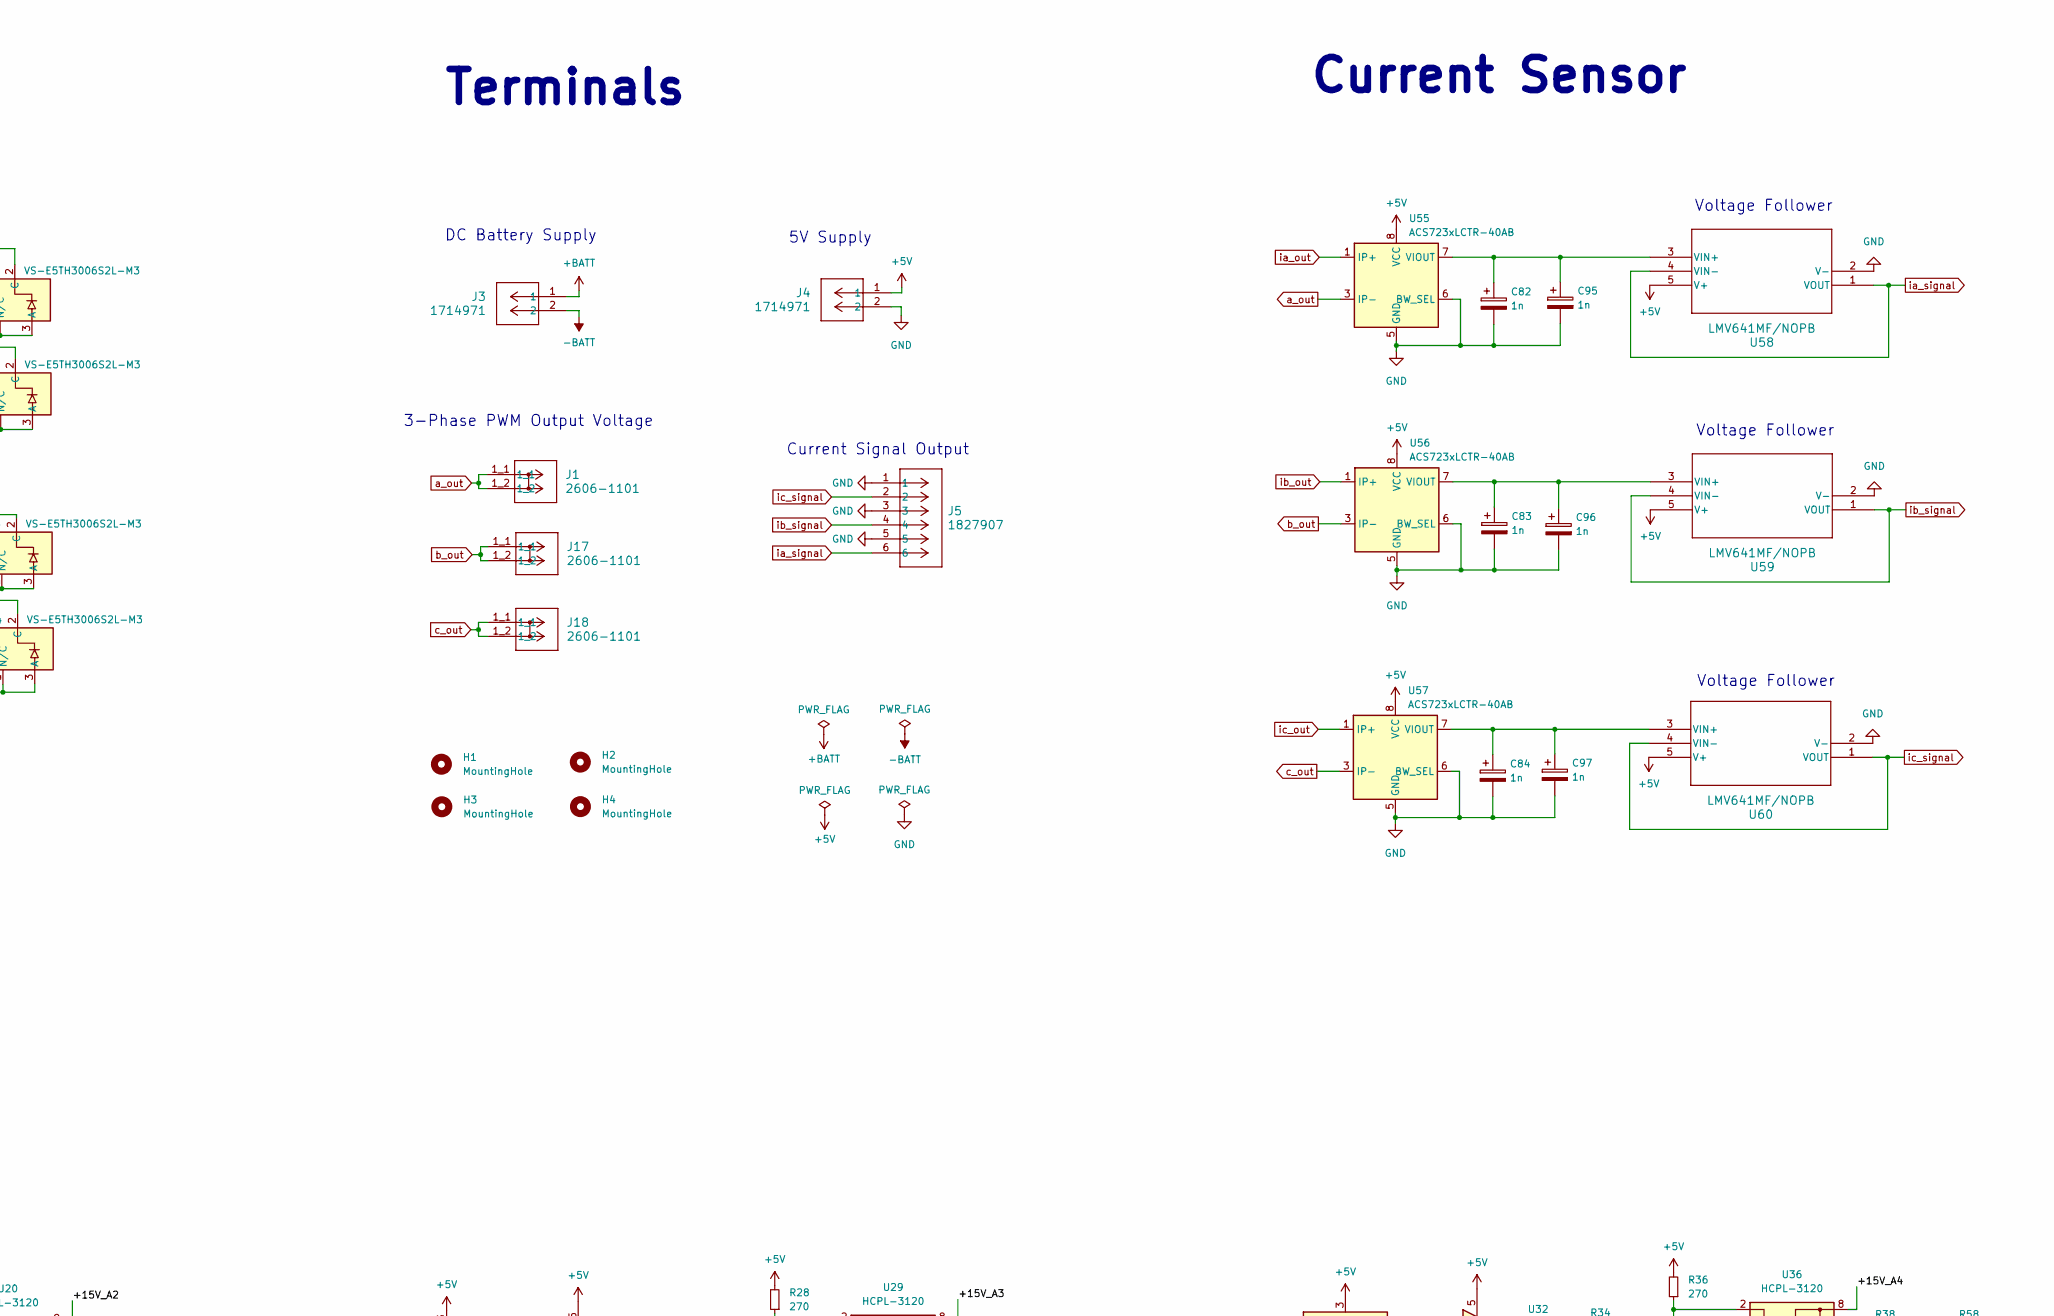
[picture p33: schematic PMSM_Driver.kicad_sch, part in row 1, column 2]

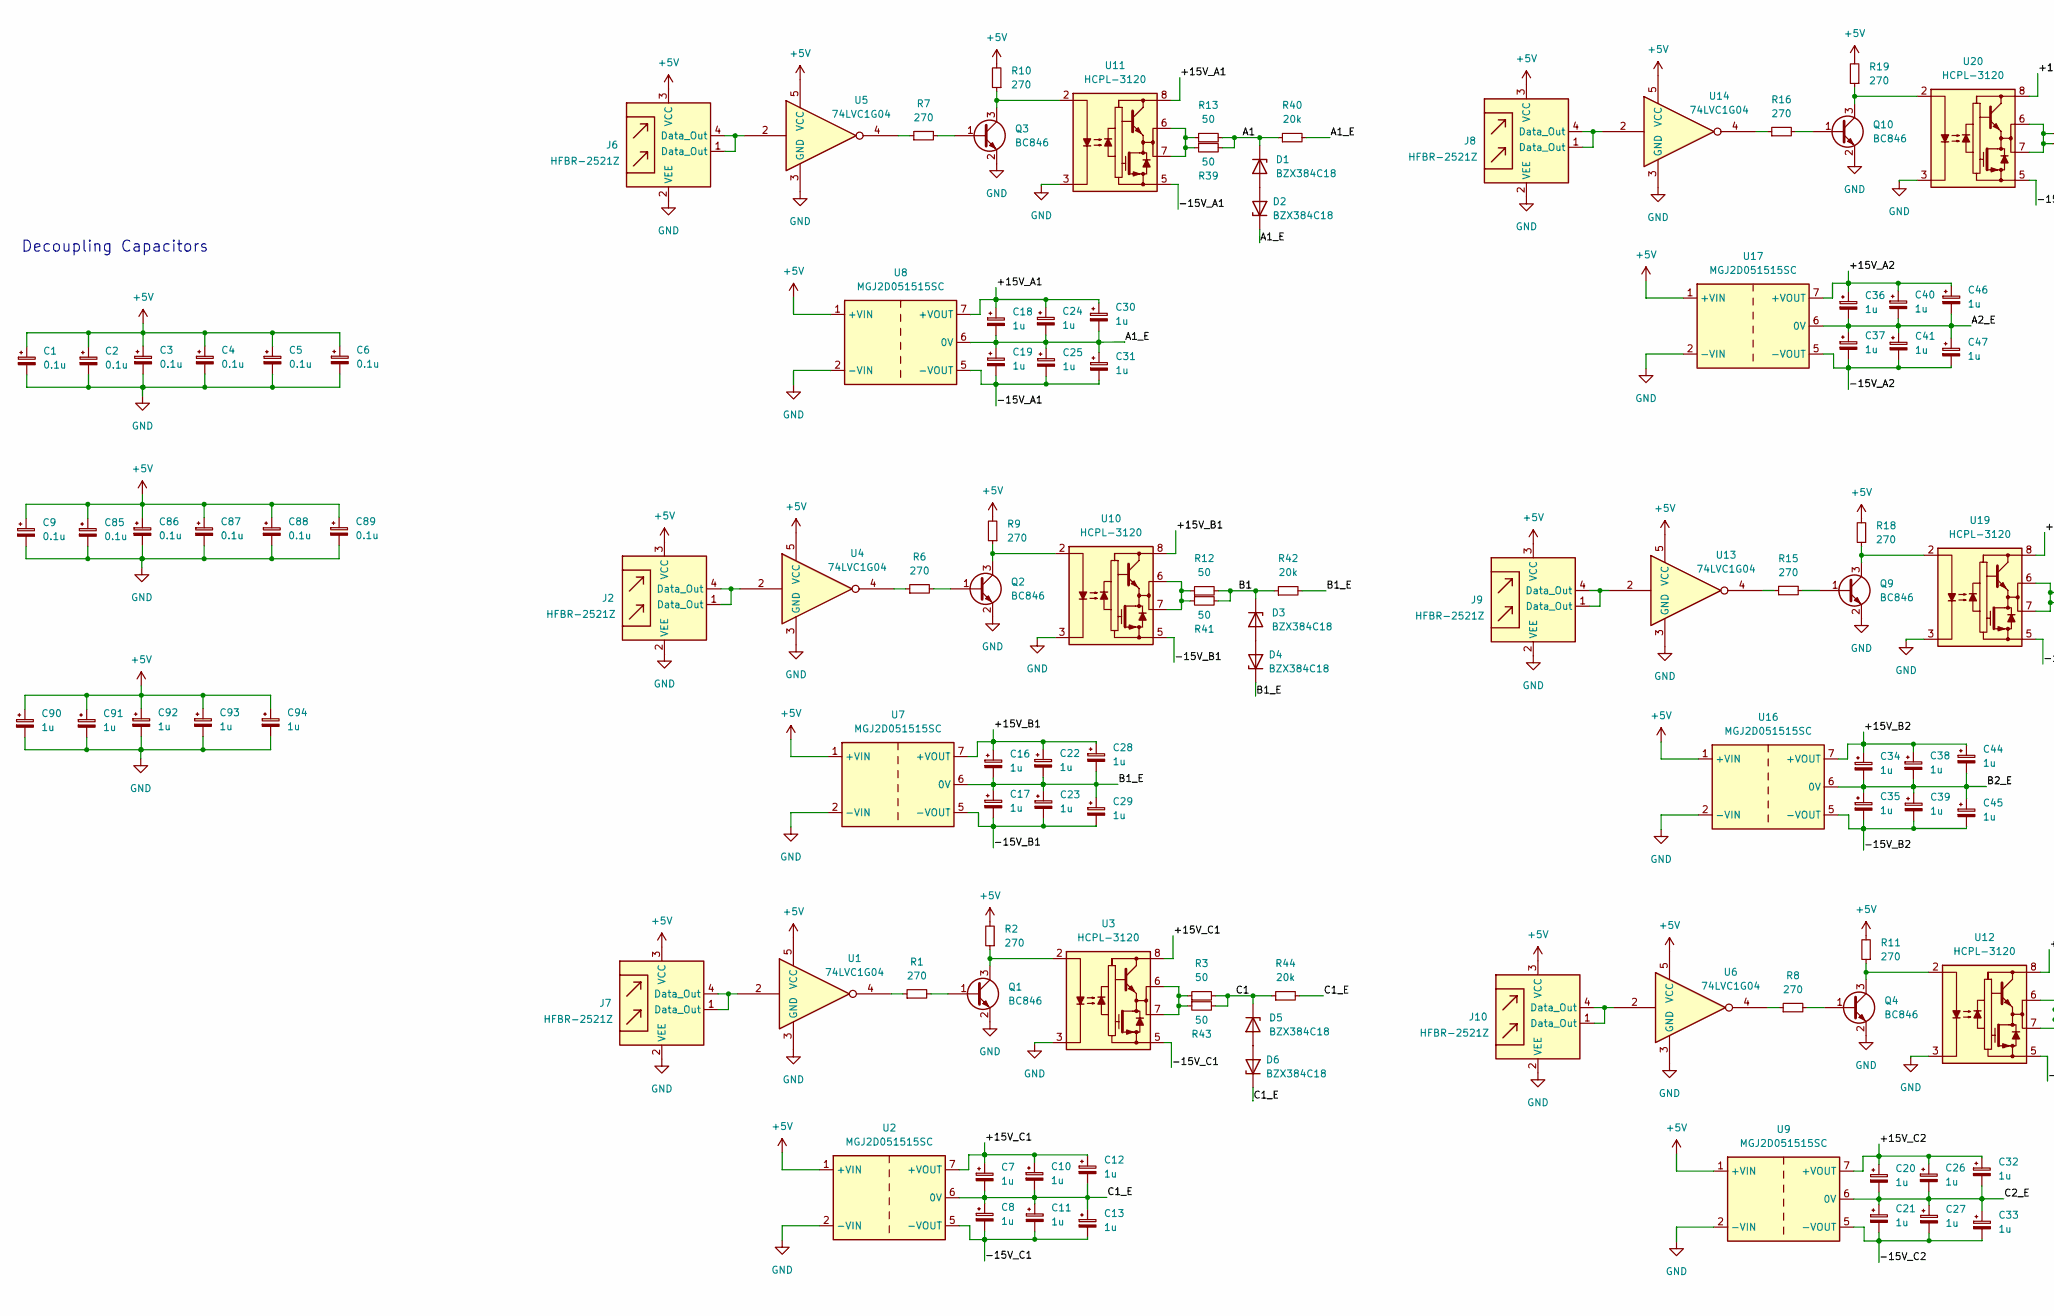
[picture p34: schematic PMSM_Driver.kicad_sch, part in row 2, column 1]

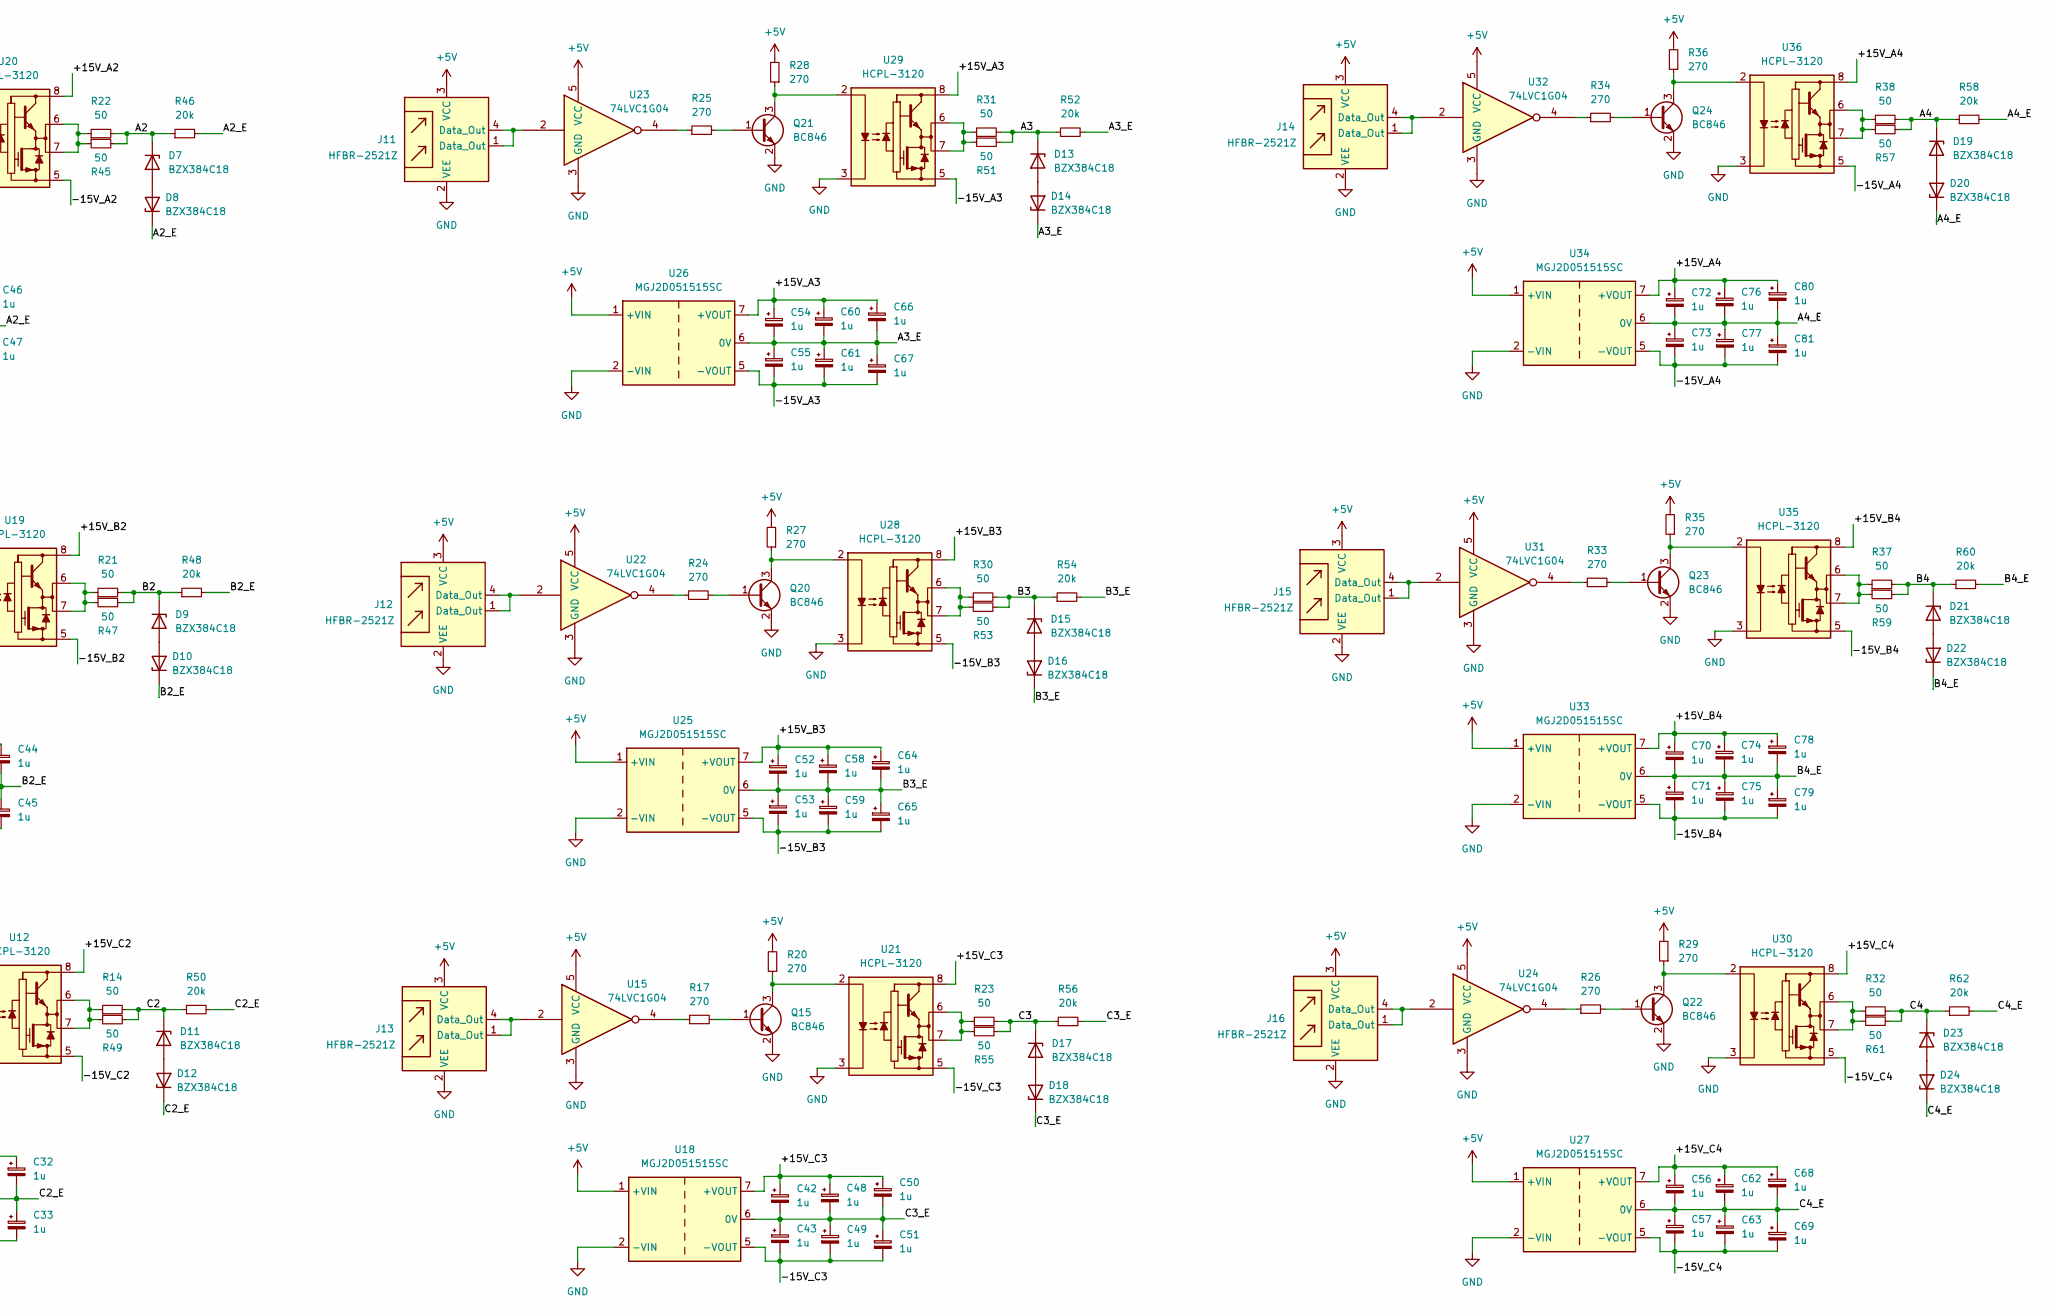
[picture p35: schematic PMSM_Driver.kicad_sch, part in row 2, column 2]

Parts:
C1, C2, C3, C4, C5, C6, C9, C85, C86, C87, C88, C89: 0.1u; C_1206_3216Metric
C7, C8, C10, C11, C12, C13, C16, C17, C18, C19, C20, C21, C22, C23, C24, C25, C26, C27, C28, C29, C30, C31, C32, C33, C34, C35, C36, C37, C38, C39, C40, C41, C42, C43, C44, C45, C46, C47, C48, C49, C50, C51, C52, C53, C54, C55, C56, C57, C58, C59, C60, C61, C62, C63, C64, C65, C66, C67, C68, C69, C70, C71, C72, C73, C74, C75, C76, C77, C78, C79, C80, C81, C90, C91, C92, C93, C94: 1u; C_1206_3216Metric
C14, C15: 22u; CP_Elec_16x17.5
C82, C83, C84, C95, C96, C97: 1n; C_1206_3216Metric
D1, D2, D3, D4, D5, D6, D7, D8, D9, D10, D11, D12, D13, D14, D15, D16, D17, D18, D19, D20, D21, D22, D23, D24: BZX384C18; D_SOD-323
H1, H2, H3, H4: MountingHole; MountingHole_3.2mm_M3_Pad_Via
J1, J17, J18: 2606-1101; CONN_2606-1101_WAG
J2, J6, J7, J8, J9, J10, J11, J12, J13, J14, J15, J16: HFBR-2521Z; Broadcom_AFBR-16xxZ_Horizontal
J3, J4: 1714971; CONN_1714971_PXC
J5: 1827907; CONN_1827907
Q1, Q2, Q3, Q4, Q9, Q10, Q15, Q20, Q21, Q22, Q23, Q24: BC846; SOT-23
Q5, Q6, Q7, Q8, Q11, Q12, Q13, Q14, Q16, Q17, Q18, Q19: RGCL60TK60; TO-3P-3_Vertical
R1, R2, R6, R7, R8, R9, R10, R11, R15, R16, R17, R18, R19, R20, R24, R25, R26, R27, R28, R29, R33, R34, R35, R36: 270; R_1206_3216Metric
R3, R12, R13, R14, R21, R22, R23, R30, R31, R32, R37, R38, R39, R41, R43, R45, R47, R49, R51, R53, R55, R57, R59, R61: 50; R_1206_3216Metric
R4, R5, R40, R42, R44, R46, R48, R50, R52, R54, R56, R58, R60, R62: 20k; R_1206_3216Metric
U1, U4, U5, U6, U13, U14, U15, U22, U23, U24, U31, U32: 74LVC1G04; SOT-23-5
U2, U7, U8, U9, U16, U17, U18, U25, U26, U27, U33, U34: MGJ2D051515SC; Converter_DCDC_Murata_MGJ2DxxxxxxSC_THT
U3, U10, U11, U12, U19, U20, U21, U28, U29, U30, U35, U36: HCPL-3120; DIP-8_W8.89mm_SMDSocket_LongPads
U37, U38, U39, U40, U41, U42, U43, U44, U45, U46, U47, U48, U49, U50, U51, U52, U53, U54: VS-E5TH3006S2L-M3; TO-263-2
U55, U56, U57: ACS723xLCTR-40AB; SOIC-8_3.9x4.9mm_P1.27mm
U58, U59, U60: LMV641MF/NOPB; DBV5_TEX

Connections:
+5V: C1.1, C2.1, C3.1, C4.1, C5.1, C6.1, C9.1, C85.1, C86.1, C87.1, C88.1, C89.1, C90.1, C91.1, C92.1, C93.1, C94.1, J2.3 (VCC), J4.1, J6.3 (VCC), J7.3 (VCC), J8.3 (VCC), J9.3 (VCC), J10.3 (VCC), J11.3 (VCC), J12.3 (VCC), J13.3 (VCC), J14.3 (VCC), J15.3 (VCC), J16.3 (VCC), R2.2, R9.2, R10.2, R11.2, R18.2, R19.2, R20.2, R27.2, R28.2, R29.2, R35.2, R36.2, U1.5 (VCC), U2.1 (+VIN), U4.5 (VCC), U5.5 (VCC), U6.5 (VCC), U7.1 (+VIN), U8.1 (+VIN), U9.1 (+VIN), U13.5 (VCC), U14.5 (VCC), U15.5 (VCC), U16.1 (+VIN), U17.1 (+VIN), U18.1 (+VIN), U22.5 (VCC), U23.5 (VCC), U24.5 (VCC), U25.1 (+VIN), U26.1 (+VIN), U27.1 (+VIN), U31.5 (VCC), U32.5 (VCC), U33.1 (+VIN), U34.1 (+VIN), U55.8 (VCC), U56.8 (VCC), U57.8 (VCC), U58.5 (V+), U59.5 (V+), U60.5 (V+)
+BATT: C14.1, J3.1, Q5.2 (C), Q11.2 (C), Q16.2 (C), R4.1, U43.2 (C), U47.2 (C), U51.2 (C)
-BATT: C15.2, C56.2, C57.1, C62.2, C63.1, C68.2, C69.1, C70.2, C71.1, C72.2, C73.1, C74.2, C75.1, C76.2, C77.1, C78.2, C79.1, C80.2, C81.1, D20.1 (K), D22.1 (K), D24.1 (K), J3.2, Q8.3 (E), Q14.3 (E), Q19.3 (E), R5.2, R58.2, R60.2, R62.2, U27.6 (0V), U33.6 (0V), U34.6 (0V), U46.1 (N/C), U46.3 (A), U50.1 (N/C), U50.3 (A), U54.1 (N/C), U54.3 (A)
/+15V_A1: C18.1, C24.1, C30.1, U8.7 (+VOUT), U11.8 (VCC)
/+15V_A2: C36.1, C40.1, C46.1, U17.7 (+VOUT), U20.8 (VCC)
/+15V_A3: C54.1, C60.1, C66.1, U26.7 (+VOUT), U29.8 (VCC)
/+15V_A4: C72.1, C76.1, C80.1, U34.7 (+VOUT), U36.8 (VCC)
/+15V_B1: C16.1, C22.1, C28.1, U7.7 (+VOUT), U10.8 (VCC)
/+15V_B2: C34.1, C38.1, C44.1, U16.7 (+VOUT), U19.8 (VCC)
/+15V_B3: C52.1, C58.1, C64.1, U25.7 (+VOUT), U28.8 (VCC)
/+15V_B4: C70.1, C74.1, C78.1, U33.7 (+VOUT), U35.8 (VCC)
/+15V_C1: C7.1, C10.1, C12.1, U2.7 (+VOUT), U3.8 (VCC)
/+15V_C2: C20.1, C26.1, C32.1, U9.7 (+VOUT), U12.8 (VCC)
/+15V_C3: C42.1, C48.1, C50.1, U18.7 (+VOUT), U21.8 (VCC)
/+15V_C4: C56.1, C62.1, C68.1, U27.7 (+VOUT), U30.8 (VCC)
/-15V_A1: C19.2, C25.2, C31.2, U8.5 (-VOUT), U11.5 (VEE)
/-15V_A2: C37.2, C41.2, C47.2, U17.5 (-VOUT), U20.5 (VEE)
/-15V_A3: C55.2, C61.2, C67.2, U26.5 (-VOUT), U29.5 (VEE)
/-15V_A4: C73.2, C77.2, C81.2, U34.5 (-VOUT), U36.5 (VEE)
/-15V_B1: C17.2, C23.2, C29.2, U7.5 (-VOUT), U10.5 (VEE)
/-15V_B2: C35.2, C39.2, C45.2, U16.5 (-VOUT), U19.5 (VEE)
/-15V_B3: C53.2, C59.2, C65.2, U25.5 (-VOUT), U28.5 (VEE)
/-15V_B4: C71.2, C75.2, C79.2, U33.5 (-VOUT), U35.5 (VEE)
/-15V_C1: C8.2, C11.2, C13.2, U2.5 (-VOUT), U3.5 (VEE)
/-15V_C2: C21.2, C27.2, C33.2, U9.5 (-VOUT), U12.5 (VEE)
/-15V_C3: C43.2, C49.2, C51.2, U18.5 (-VOUT), U21.5 (VEE)
/-15V_C4: C57.2, C63.2, C69.2, U27.5 (-VOUT), U30.5 (VEE)
/A1: D1.1 (K), Q5.1 (G), R13.2, R39.2, R40.1
/A1_E: C18.2, C19.1, C24.2, C25.1, C30.2, C31.1, D2.1 (K), Q5.3 (E), Q6.2 (C), R40.2, U8.6 (0V), U37.2 (C), U43.1 (N/C), U43.3 (A), U44.2 (C)
/A2: D7.1 (K), Q6.1 (G), R22.2, R45.2, R46.1
/A3: D13.1 (K), Q7.1 (G), R31.2, R51.2, R52.1
/A3_E: C54.2, C55.1, C60.2, C61.1, C66.2, C67.1, D14.1 (K), Q7.3 (E), Q8.2 (C), R52.2, U26.6 (0V), U38.1 (N/C), U38.3 (A), U45.1 (N/C), U45.3 (A), U46.2 (C)
/A4: D19.1 (K), Q8.1 (G), R38.2, R57.2, R58.1
/B1: D3.1 (K), Q11.1 (G), R12.2, R41.2, R42.1
/B1_E: C16.2, C17.1, C22.2, C23.1, C28.2, C29.1, D4.1 (K), Q11.3 (E), Q12.2 (C), R42.2, U7.6 (0V), U39.2 (C), U47.1 (N/C), U47.3 (A), U48.2 (C)
/B2: D9.1 (K), Q12.1 (G), R21.2, R47.2, R48.1
/B3: D15.1 (K), Q13.1 (G), R30.2, R53.2, R54.1
/B3_E: C52.2, C53.1, C58.2, C59.1, C64.2, C65.1, D16.1 (K), Q13.3 (E), Q14.2 (C), R54.2, U25.6 (0V), U40.1 (N/C), U40.3 (A), U49.1 (N/C), U49.3 (A), U50.2 (C)
/B4: D21.1 (K), Q14.1 (G), R37.2, R59.2, R60.1
/C1: D5.1 (K), Q16.1 (G), R3.2, R43.2, R44.1
/C1_E: C7.2, C8.1, C10.2, C11.1, C12.2, C13.1, D6.1 (K), Q16.3 (E), Q17.2 (C), R44.2, U2.6 (0V), U41.2 (C), U51.1 (N/C), U51.3 (A), U52.2 (C)
/C2: D11.1 (K), Q17.1 (G), R14.2, R49.2, R50.1
/C3: D17.1 (K), Q18.1 (G), R23.2, R55.2, R56.1
/C3_E: C42.2, C43.1, C48.2, C49.1, C50.2, C51.1, D18.1 (K), Q18.3 (E), Q19.2 (C), R56.2, U18.6 (0V), U42.1 (N/C), U42.3 (A), U53.1 (N/C), U53.3 (A), U54.2 (C)
/C4: D23.1 (K), Q19.1 (G), R32.2, R61.2, R62.1
GND: C1.2, C2.2, C3.2, C4.2, C5.2, C6.2, C9.2, C82.2, C83.2, C84.2, C85.2, C86.2, C87.2, C88.2, C89.2, C90.2, C91.2, C92.2, C93.2, C94.2, C95.2, C96.2, C97.2, J2.2 (VEE), J4.2, J5.1, J5.3, J5.5, J6.2 (VEE), J7.2 (VEE), J8.2 (VEE), J9.2 (VEE), J10.2 (VEE), J11.2 (VEE), J12.2 (VEE), J13.2 (VEE), J14.2 (VEE), J15.2 (VEE), J16.2 (VEE), Q1.2 (E), Q2.2 (E), Q3.2 (E), Q4.2 (E), Q9.2 (E), Q10.2 (E), Q15.2 (E), Q20.2 (E), Q21.2 (E), Q22.2 (E), Q23.2 (E), Q24.2 (E), U1.3 (GND), U2.2 (-VIN), U3.3 (C), U4.3 (GND), U5.3 (GND), U6.3 (GND), U7.2 (-VIN), U8.2 (-VIN), U9.2 (-VIN), U10.3 (C), U11.3 (C), U12.3 (C), U13.3 (GND), U14.3 (GND), U15.3 (GND), U16.2 (-VIN), U17.2 (-VIN), U18.2 (-VIN), U19.3 (C), U20.3 (C), U21.3 (C), U22.3 (GND), U23.3 (GND), U24.3 (GND), U25.2 (-VIN), U26.2 (-VIN), U27.2 (-VIN), U28.3 (C), U29.3 (C), U30.3 (C), U31.3 (GND), U32.3 (GND), U33.2 (-VIN), U34.2 (-VIN), U35.3 (C), U36.3 (C), U55.5 (GND), U55.6 (BW_SEL), U56.5 (GND), U56.6 (BW_SEL), U57.5 (GND), U57.6 (BW_SEL), U58.2 (V-), U59.2 (V-), U60.2 (V-)
GNDREF: C14.2, C15.1, R4.2, R5.1, U37.1 (N/C), U37.3 (A), U38.2 (C), U39.1 (N/C), U39.3 (A), U40.2 (C), U41.1 (N/C), U41.3 (A), U42.2 (C)
unnamed: D1.2 (A), D2.2 (A)
unnamed: D3.2 (A), D4.2 (A)
unnamed: D5.2 (A), D6.2 (A)
unnamed: D7.2 (A), D8.2 (A)
unnamed: D9.2 (A), D10.2 (A)
unnamed: D11.2 (A), D12.2 (A)
unnamed: D13.2 (A), D14.2 (A)
unnamed: D15.2 (A), D16.2 (A)
unnamed: D17.2 (A), D18.2 (A)
unnamed: D19.2 (A), D20.2 (A)
unnamed: D21.2 (A), D22.2 (A)
unnamed: D23.2 (A), D24.2 (A)
unnamed: J2.1 (Data_Out), J2.4 (Data_Out), U4.2
unnamed: J6.1 (Data_Out), J6.4 (Data_Out), U5.2
unnamed: J7.1 (Data_Out), J7.4 (Data_Out), U1.2
unnamed: J8.1 (Data_Out), J8.4 (Data_Out), U14.2
unnamed: J9.1 (Data_Out), J9.4 (Data_Out), U13.2
unnamed: J10.1 (Data_Out), J10.4 (Data_Out), U6.2
unnamed: J11.1 (Data_Out), J11.4 (Data_Out), U23.2
unnamed: J12.1 (Data_Out), J12.4 (Data_Out), U22.2
unnamed: J13.1 (Data_Out), J13.4 (Data_Out), U15.2
unnamed: J14.1 (Data_Out), J14.4 (Data_Out), U32.2
unnamed: J15.1 (Data_Out), J15.4 (Data_Out), U31.2
unnamed: J16.1 (Data_Out), J16.4 (Data_Out), U24.2
unnamed: Q1.1 (B), R1.2
unnamed: Q1.3 (C), R2.1, U3.2 (A)
unnamed: Q2.1 (B), R6.2
unnamed: Q2.3 (C), R9.1, U10.2 (A)
unnamed: Q3.1 (B), R7.2
unnamed: Q3.3 (C), R10.1, U11.2 (A)
unnamed: Q4.1 (B), R8.2
unnamed: Q4.3 (C), R11.1, U12.2 (A)
unnamed: Q9.1 (B), R15.2
unnamed: Q9.3 (C), R18.1, U19.2 (A)
unnamed: Q10.1 (B), R16.2
unnamed: Q10.3 (C), R19.1, U20.2 (A)
unnamed: Q15.1 (B), R17.2
unnamed: Q15.3 (C), R20.1, U21.2 (A)
unnamed: Q20.1 (B), R24.2
unnamed: Q20.3 (C), R27.1, U28.2 (A)
unnamed: Q21.1 (B), R25.2
unnamed: Q21.3 (C), R28.1, U29.2 (A)
unnamed: Q22.1 (B), R26.2
unnamed: Q22.3 (C), R29.1, U30.2 (A)
unnamed: Q23.1 (B), R33.2
unnamed: Q23.3 (C), R35.1, U35.2 (A)
unnamed: Q24.1 (B), R34.2
unnamed: Q24.3 (C), R36.1, U36.2 (A)
unnamed: R1.1, U1.4
unnamed: R3.1, R43.1, U3.6 (VO), U3.7 (VO)
unnamed: R6.1, U4.4
unnamed: R7.1, U5.4
unnamed: R8.1, U6.4
unnamed: R12.1, R41.1, U10.6 (VO), U10.7 (VO)
unnamed: R13.1, R39.1, U11.6 (VO), U11.7 (VO)
unnamed: R14.1, R49.1, U12.6 (VO), U12.7 (VO)
unnamed: R15.1, U13.4
unnamed: R16.1, U14.4
unnamed: R17.1, U15.4
unnamed: R21.1, R47.1, U19.6 (VO), U19.7 (VO)
unnamed: R22.1, R45.1, U20.6 (VO), U20.7 (VO)
unnamed: R23.1, R55.1, U21.6 (VO), U21.7 (VO)
unnamed: R24.1, U22.4
unnamed: R25.1, U23.4
unnamed: R26.1, U24.4
unnamed: R30.1, R53.1, U28.6 (VO), U28.7 (VO)
unnamed: R31.1, R51.1, U29.6 (VO), U29.7 (VO)
unnamed: R32.1, R61.1, U30.6 (VO), U30.7 (VO)
unnamed: R33.1, U31.4
unnamed: R34.1, U32.4
unnamed: R37.1, R59.1, U35.6 (VO), U35.7 (VO)
unnamed: R38.1, R57.1, U36.6 (VO), U36.7 (VO)
unnamed: C82.1, C95.1, U55.7 (VIOUT), U58.3 (VIN+)
unnamed: C83.1, C96.1, U56.7 (VIOUT), U59.3 (VIN+)
unnamed: C84.1, C97.1, U57.7 (VIOUT), U60.3 (VIN+)
a_out: J1.1_1, J1.1_2, U55.3 (IP-), U55.4 (IP-)
b_out: J17.1_1, J17.1_2, U56.3 (IP-), U56.4 (IP-)
c_out: J18.1_1, J18.1_2, U57.3 (IP-), U57.4 (IP-)
ia_out: C36.2, C37.1, C40.2, C41.1, C46.2, C47.1, D8.1 (K), Q6.3 (E), Q7.2 (C), R46.2, U17.6 (0V), U44.1 (N/C), U44.3 (A), U45.2 (C), U55.1 (IP+), U55.2 (IP+)
ia_signal: J5.6, U58.1 (VOUT), U58.4 (VIN-)
ib_out: C34.2, C35.1, C38.2, C39.1, C44.2, C45.1, D10.1 (K), Q12.3 (E), Q13.2 (C), R48.2, U16.6 (0V), U48.1 (N/C), U48.3 (A), U49.2 (C), U56.1 (IP+), U56.2 (IP+)
ib_signal: J5.4, U59.1 (VOUT), U59.4 (VIN-)
ic_out: C20.2, C21.1, C26.2, C27.1, C32.2, C33.1, D12.1 (K), Q17.3 (E), Q18.2 (C), R50.2, U9.6 (0V), U52.1 (N/C), U52.3 (A), U53.2 (C), U57.1 (IP+), U57.2 (IP+)
ic_signal: J5.2, U60.1 (VOUT), U60.4 (VIN-)

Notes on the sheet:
Voltage Follower
Gate Drive
3-Phase Diode-Clamped Three-Level Inverter
Terminals
DC Battery Supply
Decoupling Capacitors
5V Supply
Current Signal Output
3-Phase PWM Output Voltage
Current Sensor

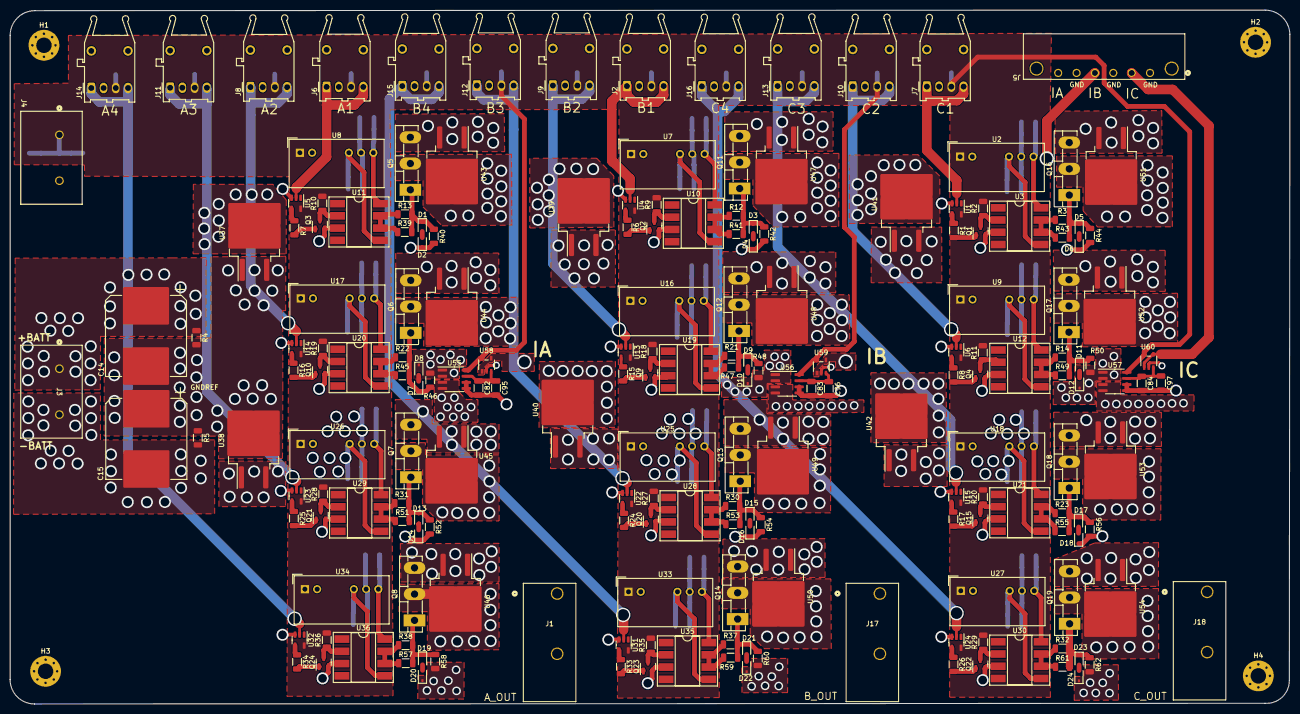
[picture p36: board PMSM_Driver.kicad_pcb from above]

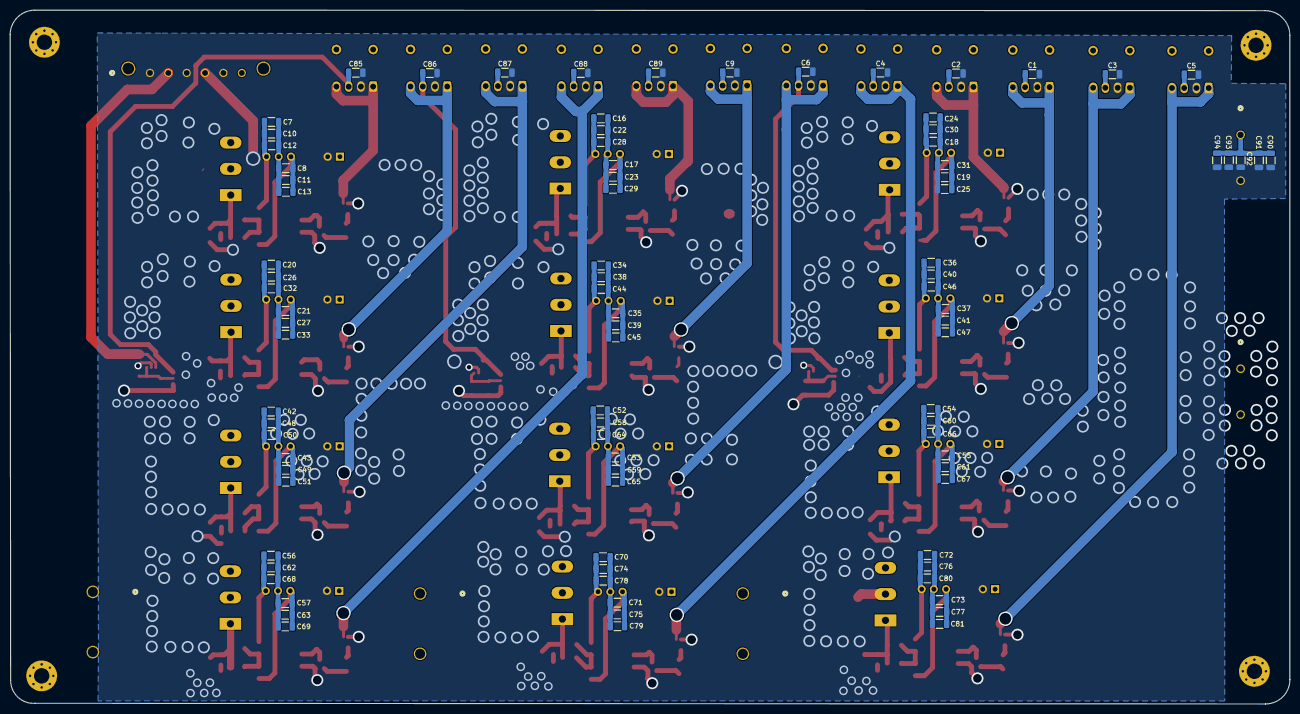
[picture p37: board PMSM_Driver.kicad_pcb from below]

Board: 4 copper layers, 265.6 x 144.0 mm, 289 parts (89 on the bottom side), 131 nets.

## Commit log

2023-11-28 modified the schematic and PCB layout, updated datasheet and BOM
    [BOM.xlsx, FYP Timetable.xlsx, PMSM_Driver.kicad_pcb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]
2023-12-02 update on PCB layout
    [BOM.xlsx, PMSM_Driver.kicad_pcb, PMSM_Driver.kicad_sch]
2023-12-02 updated the PCB layout
    [PMSM_Driver.kicad_pcb]
2023-12-03 complete the PCB layout
    [PMSM_Driver.kicad_pcb]
2023-12-03 add single buffers to signal output, update layout
    [BOM.xlsx, PMSM_Driver.kicad_pcb, PMSM_Driver.kicad_sch]
2023-12-05 modified single buffer to voltage follower, modification on gate drive protection circuit is needed
    [BOM.xlsx, PMSM_Driver.kicad_pcb, PMSM_Driver.kicad_sch]
2023-12-06 updated PCB layout: gate drive protection
    [PMSM_Driver.kicad_pcb, PMSM_Driver.kicad_sch]
2023-12-08 TBC: change trace for 10A current to filled zone
    [BOM.xlsx, PMSM_Driver.kicad_pcb, PMSM_Driver.kicad_sch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]
2023-12-09 TBC: filled zone to replece wide trace
    [PMSM_Driver.kicad_pcb]
2023-12-09 TBC: filled zone to replace 10A traces, phase-A conpleted
    [BOM.xlsx, PMSM_Driver.kicad_pcb, Pengyuan_Shu_Supplier_FYP1.xls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]
2023-12-15 TBC: modify the overlapped filled zone
    [PMSM_Driver.kicad_pcb]
2023-12-16 Filled Zone: only Phase C left
    [BOM.xlsx, PMSM_Driver.kicad_pcb, Timetable.xlsx]
2023-12-16 filled zone completed, Fiber-Optic and size of resistors need to be replaced
    [PMSM_Driver.kicad_pcb, PMSM_Driver.kicad_sch]
2023-12-17 filled zone completed, some SMD components need to be re-selected
    [BOM.xlsx, PMSM_Driver.kicad_pcb, PMSM_Driver.kicad_sch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]
2023-12-20 Final Version 1 Update
    [BOM.xlsx, PMSM_Driver.kicad_pcb, PMSM_Driver.kicad_sch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]
2023-12-21 Completed Version 1: replace bury vias to micro vias
    [PMSM_Driver.kicad_pcb, Timetable.xlsx]
2024-01-05 Completed Version 2: changed the DC-link capacitance to 2200 uF
    [BOM.xlsx, PMSM_Driver.kicad_sch, Pengyuan_Shu_Supplier_FYP3.xls]
2024-02-10 Control board project files are added, schematic in progress
    [Control_Board_Peripherals.kicad_pcb, Control_Board_Peripherals.kicad_sch, Pengyuan_Shu_Supplier_FYP3.xls]
2024-02-17 Control board PCB layout is completed.
    [Control_Board_Peripherals.kicad_pcb, Control_Board_Peripherals.kicad_sch, Pengyuan_Shu_Supplier_FYP4.xls]
2024-03-04 CCS project is added, PCB layout are updated, simulations are combined into one file, the completed version of c-script simulation is to be done.
    [Control_Board_Peripherals.kicad_pcb, Control_Board_Peripherals.kicad_sch, PMSM_Driver.kicad_sch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]
2024-03-14 Simulation updated
    [Pengyuan_Shu_Supplier_FYP3 - Farnell to Mouser (plus reorder).xls, Pengyuan_Shu_Supplier_FYP3.xls, Pengyuan_Shu_Supplier_FYP4 - Not Arrived.xls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]
2024-03-26 Disertation added
    [Timetable.xlsx]
2024-05-05 updated thesis: 6th May
    [PMSM_Driver.kicad_sch]
2024-05-08 updated thesis: 8th May
    [Control_Board_Peripherals.kicad_sch, PMSM_Driver.kicad_sch]
2024-05-10 updated thesis: 11th May
    [Actural Timetable.xlsx, Original Timetable.xlsx, Timetable.xlsx]
